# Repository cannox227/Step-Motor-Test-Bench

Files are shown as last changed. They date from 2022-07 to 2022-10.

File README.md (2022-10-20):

# Step-motor-test-bench

Step Motor Testbench is a tool made in collaboration with [ProM Facility](https://promfacility.eu/#/) which can be used to measure the __maximum power__ and the __maximum torque__ of a step motor. <br>
Notice that this is a prototype made up to validate the innovative company idea. 
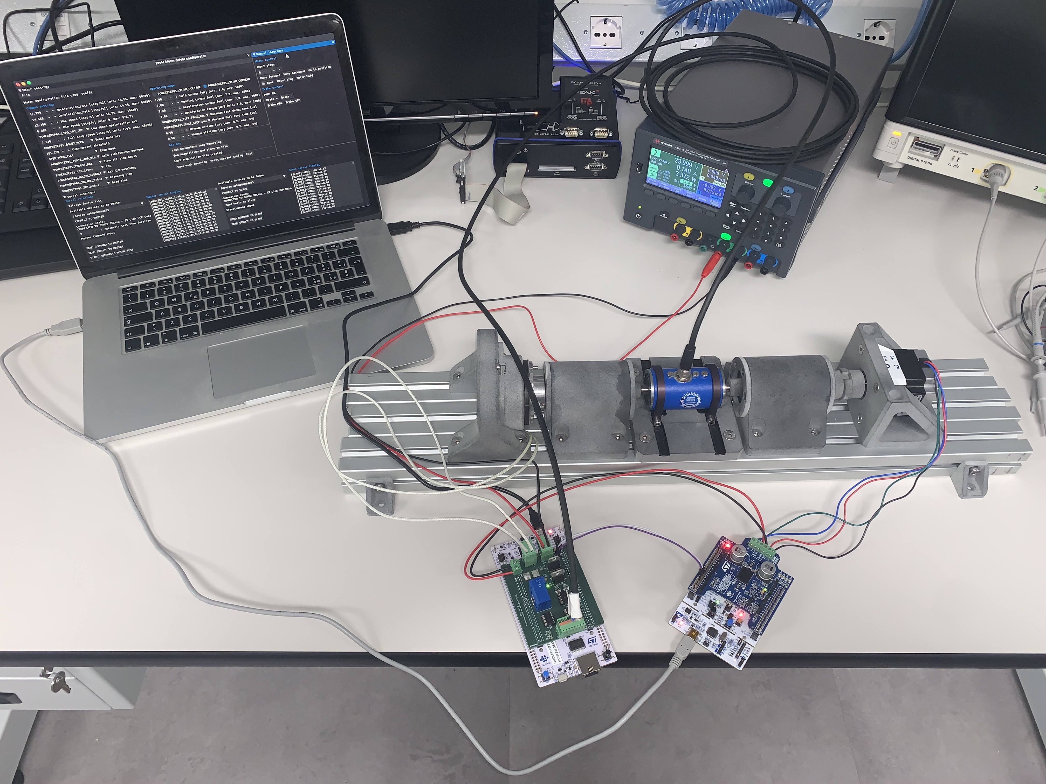
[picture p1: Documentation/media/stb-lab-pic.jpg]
stb-lab-pic


## Functionalities
1. Driving the stepper motor
2. Driving the magnetic brake
3. Measuring the involved physical quantities such as: torque, voltage and current of the motor
4. Set the motor driver parameters and show the plots related to the obtained motor curves using a GUI (Graphical User Interface)

## Main components
- Step motor (device under test)
- Torque sensor
- Magnetic brake
- Master unit made of
    - Nucleo STM32 F7 Board
    - Custom PCB to handle different voltages and conditionate the signals
- Slave unit made of
    - Nucleo STM32 F4 Board
    - STM X-NUCLEO-IHM03A1 stepper driver extension board

## System block diagram
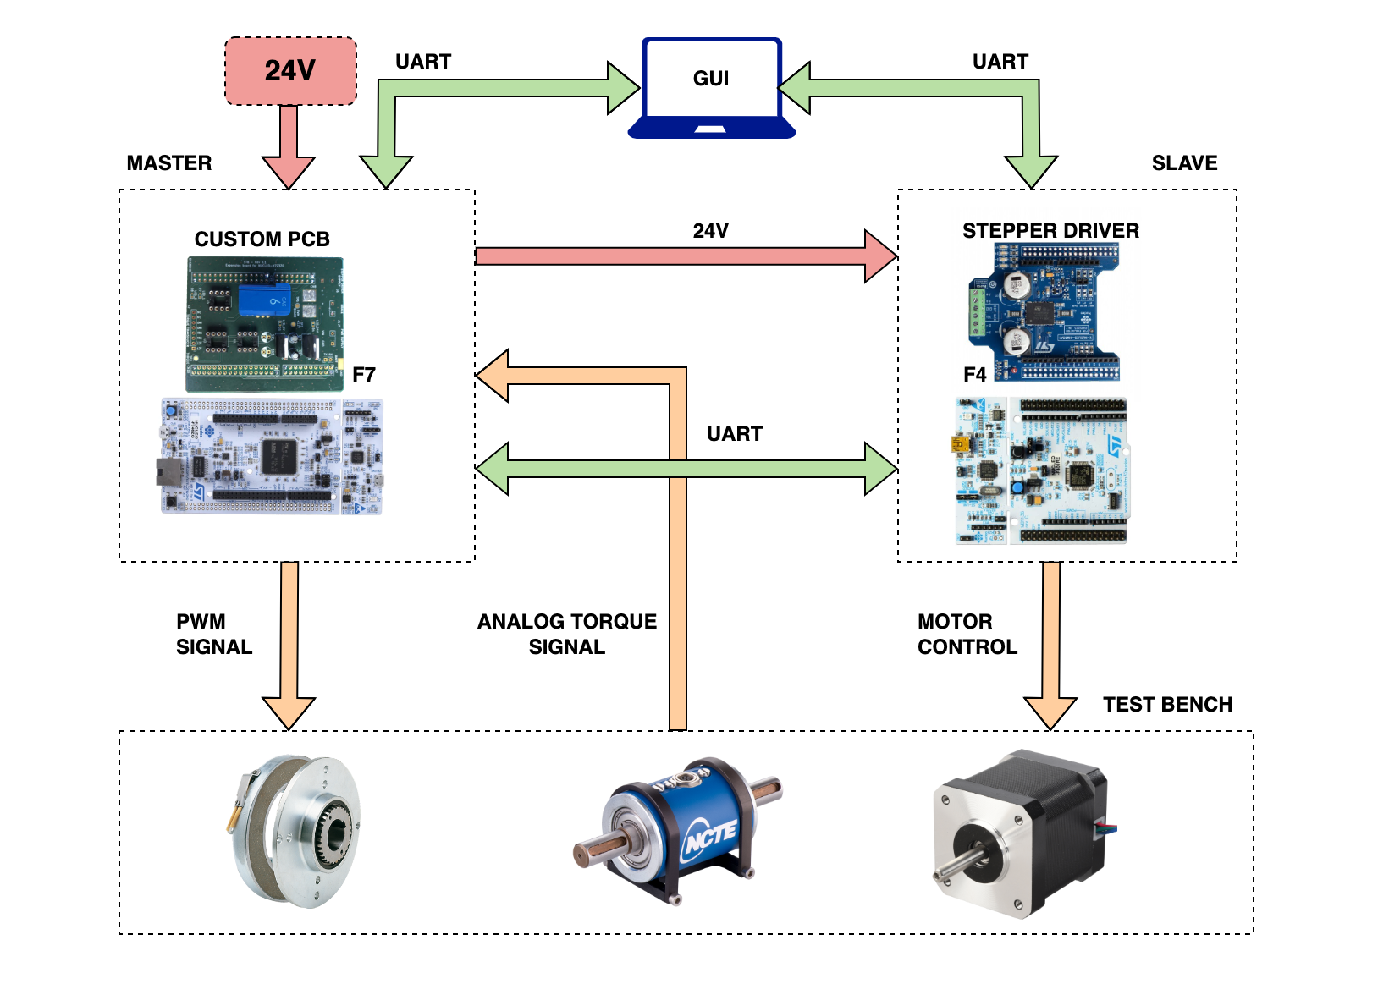
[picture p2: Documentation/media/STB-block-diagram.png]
System block diagram

## Thesis abstract
This thesis reports the work done during my internship period at ProM Facility, the company - based in Rovereto (TN) - is focused on mechanics, electronics and informatics prototyping. This work principally covers the high level software development and at the same time the baremetal firmware development to support the innovative company project. In particular, ProM Facility had the necessity to prototype a __stepper motor test bench__ for an internal usage. This measurement tool is able to determine the __maximum power__ and __maximum torque__ provided by the under test motor.

At my arrival in the company the test bench mechanical structure was already built, ensuring the connection between a magnetic brake, a torque sensor and a stepper motor. To make the prototype actually working it has been necessary to integrate the hardware development with the software one. Obtaining the characteristic curves that describes the performance of the motor has been one of the main objectives of my work, in order to get this results sensors of voltage, current and torque have been used. Moreover, a wide variety of motor driver parameters selection has been implemented, in such a way to build a custom configuration with the purpose of optimize the produced curves by operating on the single parameters. However, this curve optimization task will be studied by the future company interns.

It has also been developed a dedicated graphical user interface to let the end user interacting with the test bench, with this software it is possible to change the motor driver parameters and test it under load; on the other hand, to read the sensors values and drive the motor, two units have been projected: _master_ and _slave_. The first one is made up of a _STM Nucleo F7_ board with a custom developed _shield_, where sensors and signal conditioning circuits have been soldered. The second one, instead, is composed of a _STM Nucleo F4_ board and an expansion driver board - the _STM X-NUCLEO-IHM03A1_ - necessary to control the motor under the F4 _microcontroller_ rules.

The thesis especially describes the development process to create the graphical interface using the Python programming language and to write the firmware of the master unit. For the last one a duo formed by the STM Cube MX software and the C language has been selected. Eventually, the remaining work, consisting of the slave firmware development and the prototyping of the expansion board for the master unit, has been up to the colleague with whom I have shared the internship experience, _Lisa Santarossa_.

As planned, the project has been concluded successfully, gathering the curves of __torque-power__ based on the custom configuration chosen by the end user.

__You can find the theseis [here](/Documentation/Tommaso_Canova_STB_thesis.pdf)__

## Repo structure
    ├── 📁 Documentation    -> media and thesis
    ├── 📁 Firmware         -> slave and master units firmware
    ├── 📁 GUI              -> graphical user iterface and plot scripts
    └── 📁 Hardware         -> custom master unit expansion board kicad project

## GUI screenshots
The GUI is made up of two main windows: the first one is used to control the motor driver parameters, to test the motor under load, to communicate with both units using serial communication and to save the acquired data into a csv file. The second one is used to plot the acquired data into some.

The second one is used to read the sensors values and to plot the acquired data in a dynamic way. 

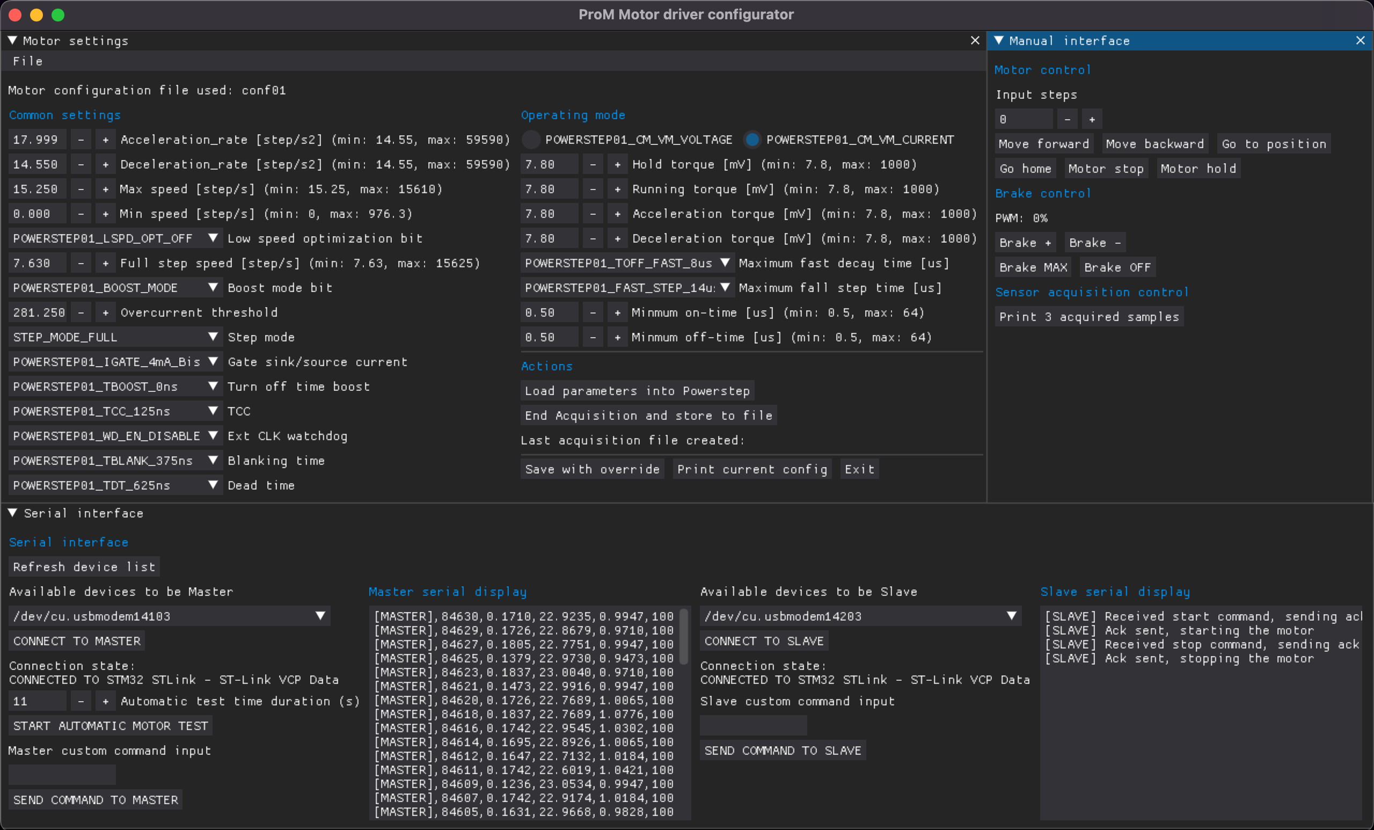
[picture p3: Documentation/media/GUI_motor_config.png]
GUI Motor config window


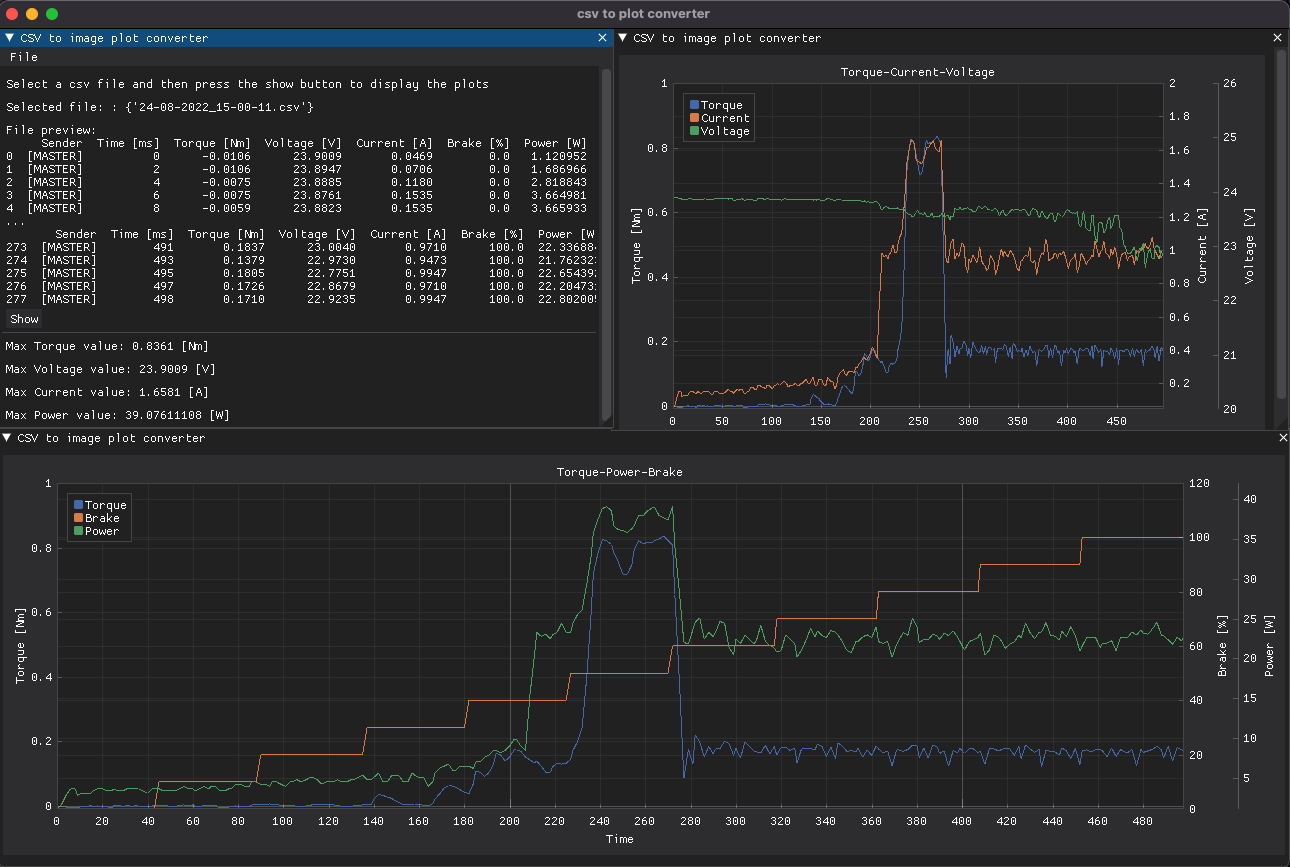
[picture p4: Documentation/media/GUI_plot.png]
GUI plot window


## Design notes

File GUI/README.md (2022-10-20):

# Stepper Testbench GUI
The GUI is made up of two main windows: the first one is used to control the motor driver parameters, to test the motor under load, to communicate with both units using serial communication and to save the acquired data into a csv file. The second one is used to plot the acquired data into some.

The second one is used to read the sensors values and to plot the acquired data in a dynamic way. 

GUI Motor config window

GUI plot window
# GUI Installation
    cd src
    pip3 install -r requirements.txt
# Usage
## Open STB motor dashboard
    python3 main.py

## Open CSV to plot handler
    python3 csv_to_plot_guy.py

## Store CSV datas into some pdf plots 
    cd csv
    python3 save_plot.py {csv_file.csv | last}

Note 1: The scripts takes one arguement which can be a csv (which contains the acquired) or the `last` keyword.
If `last` is typed, the script will take last added csv file inside `csv` folder.<br>
Note 2: The .csv file must be inside the `csv` folder and it has to respect the following format `DD_MM_YYYY_HH_MM_SS.csv`

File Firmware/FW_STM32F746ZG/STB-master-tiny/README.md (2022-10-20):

# STB master tiny
Just a fake playground to program a NUCLEO STMF4 board to test the communication logic. Nothing fancy here.

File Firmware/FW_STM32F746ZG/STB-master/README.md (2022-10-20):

# STB master
The StepperTestBench (STB) master unit is written in C using STM32CubeMX. The systems allows to control the magnetic brake and read the analog torque sensor. 
The master unit communicates both with the GUI and the slave unit using the serial UART protocol.

stb-schema

## Code Flowchart
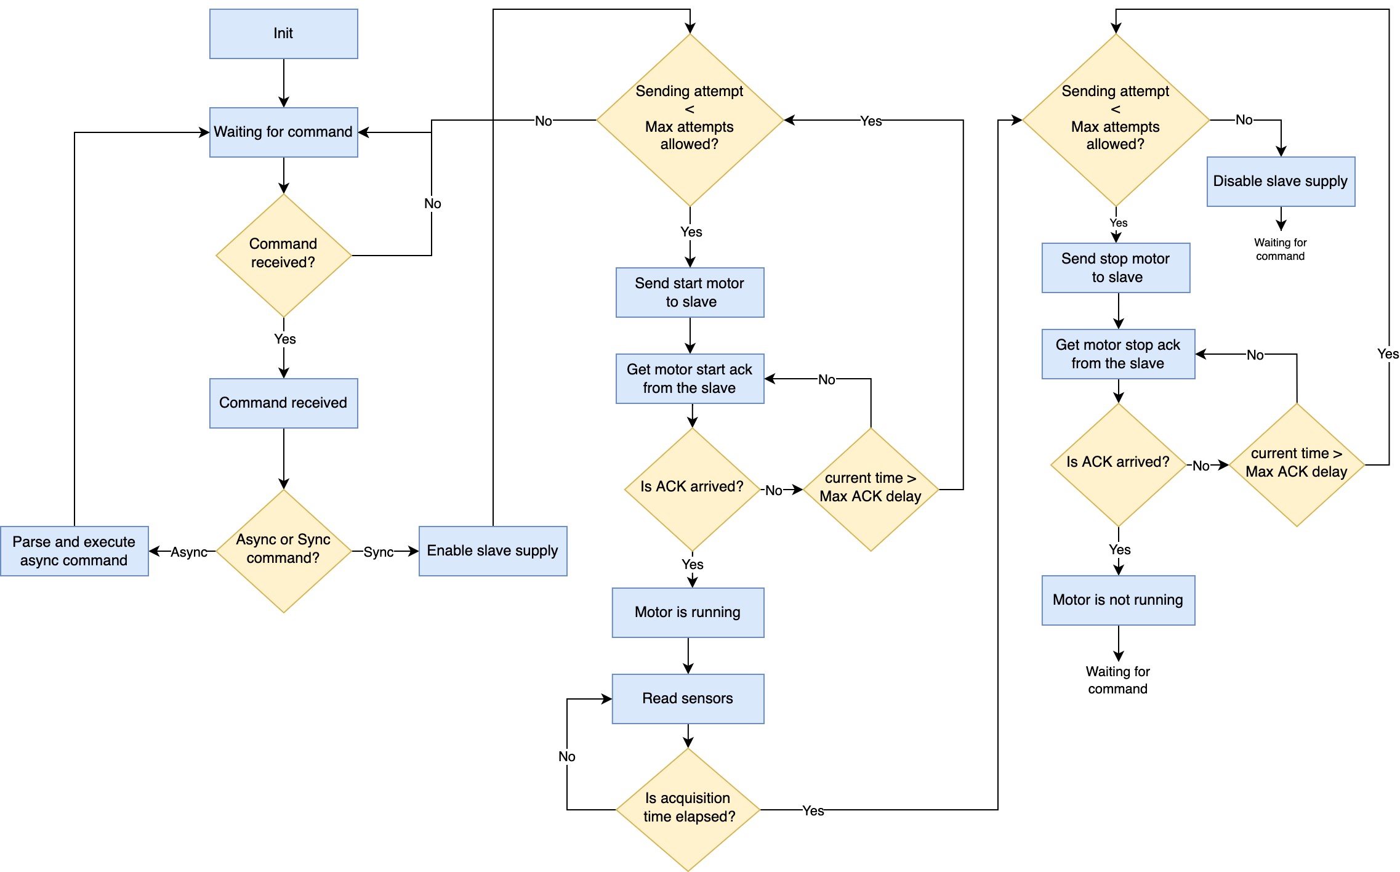
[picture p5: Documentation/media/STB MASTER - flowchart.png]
stb-master-flowchart


A finite-state machine (FSM) model has been chosen to describe and formalize the master unit be- haviour. Since the device has to deal with an __automatic test__ and a __manual test__, the FSM is basically divided in two sequential branches. The first one is aimed to handle a synchronous event (the automatic test), where every action of the unit is time dependent and at the same time is slave- message subordinate. To give an example, in the first branch it is not possible to read the analog sensors before the receiving of a `start-motor` message acknowledgment from the slave. On the other hand the second branch is __slave-independent__, so it is possible to manage a braking command or a reading sensors in an _asynchronous way_, without considering the current state of the slave. To give another example, during a manual test, it is possible to read the sensors or pilot the brake even when the slave is not driving the motor, as this branch is totally slave-independent. Note that a manual test has no need to start from a specific condition, indeed when the master is not operating an automatic test, every command is interpreted as a manual test command. The entire FSM flowchart is reported in figure 5.1.
When an automatic test is launched with the GUI, the master unit sends to the slave a `start_motor` command and then waits for a fixed time in order to receive an acknowledging message from the slave to know if the motor is running. The sending and waiting operation respects a fixed timing defined by the multiplication of the macros `MAX_CMD_SEND_ATTEMPTS` and `MAX_ACK_ALLOWED_DELAY_MS`. If the slave does not respect this timing, the test must be re-launched by the GUI; otherwise if it is respected, the master starts to acquire the ADCs values and sends them to the GUI, while piloting gradually the brake, until the total duration of the test. Then the brake is released and a `stop_motor` command is sent with the same acknowledgement procedure.

## Build and flash the project
Open the project with VSCode and install the [stm32-for-vscode](https://marketplace.visualstudio.com/items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,STM32%20for%20VSCode%20configuration%20file.) extension.

The you can just use the Build button and the Flash one to upload the firmware.
build-flash-gif

_This gif is taken from the stm32-for-vscode extension_

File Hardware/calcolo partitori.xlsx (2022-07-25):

Dispositivo | Vmin | Vmax | V_max_scelta | V_in_max_adc | V_in_max_adc/V_max_scelta | R1 | R2 | R2/(R1+R2) | V_in_adc_post_partitore
Torsiometro | 0.5 | 4.5 | 5 | 3.3 | 0.66 | 3.3 | 6.2 | 0.6526315789 | 3.263157895 | VMAX
Sensore di corrente | 0.375 | 4.625 | 5 | 3.3 | 0.66 | 3.3 | 6.2 | 0.6526315789 | 3.263157895
Tensione banco/batteria | 0 | 24 | 24 | 3.3 | 0.1375 | 6.2 | 1 | 0.1388888889 | 3.333333333 | R1

OpAmp | R1 | R2 | 2*R1/(R2+2R1) | Vmax_adc/V_in_max |  |  |  |  |  | --------> | VOUT
-2*R1/(R2+2R1) = 0.66 | 6.8 | 8.2 | 0.623853211 | 0.66 | Torsiometro + Sensore di Corrente
 | 1 | 18 | 0.1 | 0.11 | Tensione banco/batteria |  |  |  |  | R2

 |  |  |  |  |  |  |  |  |  | GND
Torsiometro lavora a 12 |  |  |  |  |  |  |  |  |  | VMAX*R2/(R1+R2) = 3.3
30 -> 12
12 -> 5 |  |  |  |  |  |  |  |  |  | 3.3/VMAX = R2/(R1+R2)
Regolatore | vo | vref | r2 | r1 | r2/r1 | vo/vref -1
Vo = Vref*(1+r2/r1) | 12 | 1.25 | 8.6 | 1 | 8.6 | 8.6

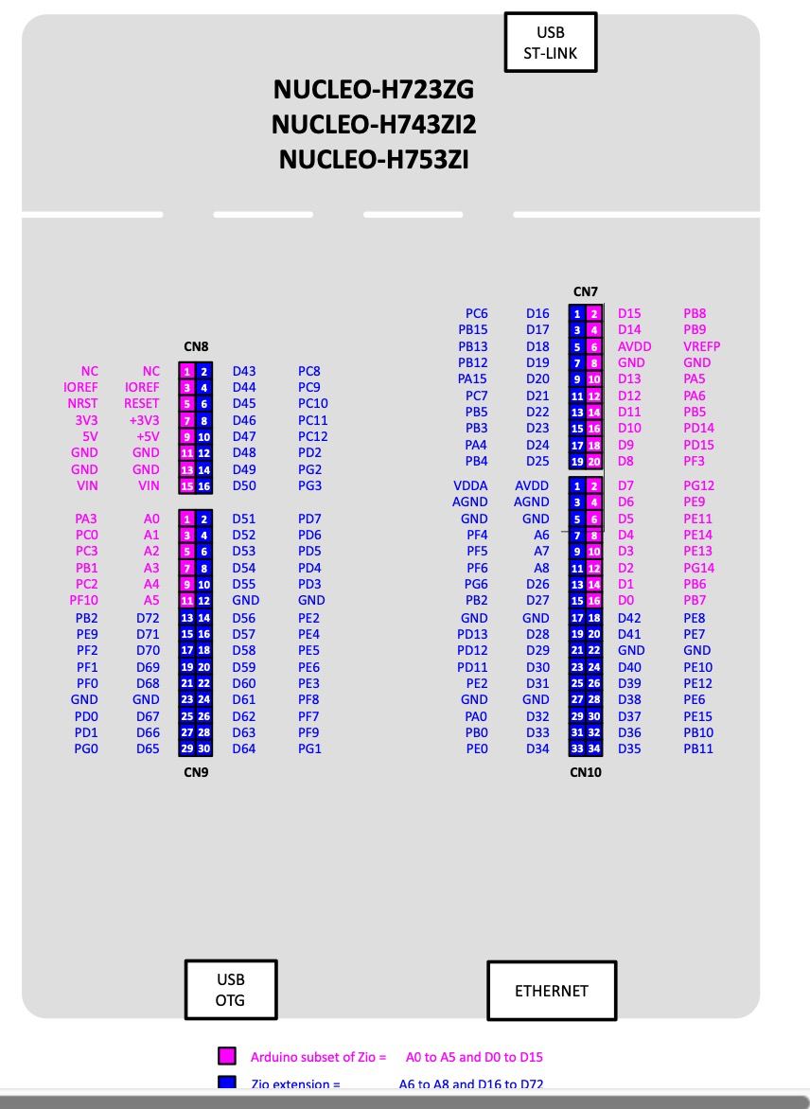
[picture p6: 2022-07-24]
Hardware/datasheets/STM32H723ZG PINOUT.jpeg

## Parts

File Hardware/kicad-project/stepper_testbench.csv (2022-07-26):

Source: | /Users/tommasocanova/Desktop/UNI/TESI/Step-Motor-Test-Bench/Hardware/kicad-project/stepper_testbench.kicad_sch
Date: | 2022 July 26, Tuesday 16:24:27
Tool: | Eeschema (6.0.2-0)
Generator: | /Applications/KiCad/KiCad.app/Contents/SharedSupport/plugins/bom_csv_grouped_by_value.py
Component Count: | 77
Individual Components:
Item | Qty | Reference(s) | Value | LibPart | Footprint | Datasheet | Spice_Netlist_Enabled | Spice_Primitive | V
 |  | C1 | 100n | Device:C | Capacitor_SMD:C_0603_1608Metric | ~
 |  | C2 | 0.1u | Device:C | Capacitor_SMD:C_0603_1608Metric | ~
 |  | C3 | 0.1u | Device:C | Capacitor_SMD:C_0603_1608Metric | ~
 |  | C4 | 100n | Device:C | Capacitor_SMD:C_0603_1608Metric | ~
 |  | C5 | 0.1u | Device:C | Capacitor_SMD:C_0603_1608Metric | ~
 |  | C6 | 100n | Device:C | Capacitor_SMD:C_0603_1608Metric | ~
 |  | C7 | 0.1u | Device:C | Capacitor_SMD:C_0603_1608Metric | ~
 |  | C8 | 0.33u | Device:C | Capacitor_SMD:C_0603_1608Metric | ~ |  |  | 25V
 |  | C9 | DNP | Device:C | Capacitor_SMD:C_0805_2012Metric | ~
 |  | C10 | 0.33u | Device:C | Capacitor_SMD:C_0603_1608Metric | ~ |  |  | 25V
 |  | C11 | 0.1u | Device:C | Capacitor_SMD:C_0603_1608Metric | ~
 |  | C12 | 0.1u | Device:C | Capacitor_SMD:C_0603_1608Metric | ~ |  |  | 25V
 |  | C13 | 0.33u_DNP | Device:C | Capacitor_THT:CP_Radial_D5.0mm_P2.50mm | ~ |  |  | 25V
 |  | C14 | 0.1u_DNP | Device:C | Capacitor_THT:CP_Radial_D5.0mm_P2.50mm | ~ |  |  | 25V
 |  | C15 | 0.33u_DNP | Device:C | Capacitor_THT:CP_Radial_D5.0mm_P2.50mm | ~ |  |  | 25V
 |  | C16 | 0.1u_DNP | Device:C | Capacitor_THT:CP_Radial_D5.0mm_P2.50mm | ~ |  |  | 25V
 |  | C17 | C | Device:C | Capacitor_SMD:C_0805_2012Metric | ~
 |  | C18 | C | Device:C | Capacitor_SMD:C_0805_2012Metric | ~
 |  | C19 | C | Device:C | Capacitor_SMD:C_0805_2012Metric | ~
 |  | CN7 | Conn_02x10_Odd_Even | Connector_Generic:Conn_02x10_Odd_Even | Connector_PinHeader_2.54mm:PinHeader_2x10_P2.54mm_Vertical | ~
 |  | CN8 | Conn_02x08_Odd_Even | Connector_Generic:Conn_02x08_Odd_Even | Connector_PinHeader_2.54mm:PinHeader_2x08_P2.54mm_Vertical | ~
 |  | CN9 | Conn_02x15_Odd_Even | Connector_Generic:Conn_02x15_Odd_Even | Connector_PinHeader_2.54mm:PinHeader_2x15_P2.54mm_Vertical | ~
 |  | CN10 | Conn_02x17_Odd_Even | Connector_Generic:Conn_02x17_Odd_Even | Connector_PinHeader_2.54mm:PinHeader_2x17_P2.54mm_Vertical | ~
 |  | D1 | DIODE | Simulation_SPICE:DIODE | Diode_SMD:D_SOD-323 | ~ | Y | D
 |  | D2 | DIODE | Simulation_SPICE:DIODE | Diode_SMD:D_SOD-323 | ~ | Y | D
 |  | D3 | D_Zener | Device:D_Zener | Diode_SMD:D_SOD-323 | ~
 |  | D4 | LED_RED | Device:LED | LED_SMD:LED_0603_1608Metric | ~
 |  | D5 | DIODE | Simulation_SPICE:DIODE | Diode_SMD:D_SOD-323 | ~ | Y | D
 |  | D6 | LED_GREEN | Device:LED | LED_SMD:LED_0603_1608Metric | ~
 |  | D7 | LED | Device:LED | LED_SMD:LED_0603_1608Metric | ~
 |  | D8 | LED | Device:LED | LED_SMD:LED_0603_1608Metric | ~
 |  | FB1 | FerriteBead | Device:FerriteBead | Resistor_SMD:R_0805_2012Metric | ~
 |  | J1 | Brake connector | Connector_Generic:Conn_01x02 | Connector_PinHeader_2.54mm:PinHeader_1x02_P2.54mm_Vertical | ~
 |  | J2 | Conn_01x08 | Connector_Generic:Conn_01x08 | Connector_PinHeader_2.54mm:PinHeader_1x08_P2.54mm_Vertical | ~
 |  | J3 | PWM module connector | Connector_Generic:Conn_01x03 | Connector_PinHeader_2.54mm:PinHeader_1x03_P2.54mm_Vertical | ~
 |  | J4 | Conn_01x02 | Connector_Generic:Conn_01x02 | Connector_PinHeader_2.54mm:PinHeader_1x02_P2.54mm_Vertical | ~
 |  | J5 | UART Connector | Connector_Generic:Conn_01x02 | Connector_PinHeader_2.54mm:PinHeader_1x02_P2.54mm_Vertical | ~
 |  | J6 | Stepper supply | Connector_Generic:Conn_01x02 | Connector_PinHeader_2.54mm:PinHeader_1x02_P2.54mm_Vertical | ~
 |  | Q1 | Q_NMOS_DGS | Device:Q_NMOS_GDS | Package_TO_SOT_SMD:TO-252-2 | ~
 |  | R1 | 10k | Device:R | Resistor_SMD:R_0603_1608Metric | ~
 |  | R2 | 0 | Device:R | Resistor_SMD:R_0603_1608Metric | ~
 |  | R3 | 47 | Device:R | Resistor_SMD:R_0603_1608Metric | ~
 |  | R4 | 0 | Device:R | Resistor_SMD:R_0603_1608Metric | ~
 |  | R5 | 0 | Device:R | Resistor_SMD:R_0603_1608Metric | ~
 |  | R6 | 10k | Device:R | Resistor_SMD:R_0603_1608Metric | ~
 |  | R7 | 330k | Device:R | Resistor_SMD:R_0603_1608Metric | ~
 |  | R8 | 620k | Device:R | Resistor_SMD:R_0603_1608Metric | ~
 |  | R9 | 10k | Device:R | Resistor_SMD:R_0603_1608Metric | ~
 |  | R10 | 330k | Device:R | Resistor_SMD:R_0603_1608Metric | ~
 |  | R11 | 620k | Device:R | Resistor_SMD:R_0603_1608Metric | ~
 |  | R12 | 10k | Device:R | Resistor_SMD:R_0603_1608Metric | ~
 |  | R13 | 620k | Device:R | Resistor_SMD:R_0603_1608Metric | ~
 |  | R14 | 100k | Device:R | Resistor_SMD:R_0603_1608Metric | ~
 |  | R15 | 0 | Device:R | Resistor_SMD:R_0603_1608Metric | ~
 |  | R16 | R | Device:R | Resistor_SMD:R_0603_1608Metric | ~
 |  | R17 | R | Device:R | Resistor_SMD:R_0603_1608Metric | ~
 |  | R18 | 510 | Device:R | Resistor_SMD:R_0603_1608Metric | ~
 |  | R19 | 330 | Device:R | Resistor_SMD:R_0603_1608Metric | ~
 |  | R20 | 5k1 | Device:R | Resistor_SMD:R_0603_1608Metric | ~
 |  | R21 | 1k | Device:R | Resistor_SMD:R_0603_1608Metric | ~
 |  | R22 | 0 | Device:R | Resistor_SMD:R_0603_1608Metric | ~
 |  | R23 | R | Device:R | Resistor_SMD:R_0603_1608Metric | ~
 |  | R24 | R | Device:R | Resistor_SMD:R_0603_1608Metric | ~
 |  | R25 | 0 | Device:R | Resistor_SMD:R_0603_1608Metric | ~
 |  | R26 | R | Device:R | Resistor_SMD:R_0603_1608Metric | ~
 |  | R27 | R | Device:R | Resistor_SMD:R_0603_1608Metric | ~
 |  | TP1 | 24V | Connector:TestPoint | TestPoint:TestPoint_Pad_D2.0mm | ~
 |  | TP2 | TORQUE | Connector:TestPoint | TestPoint:TestPoint_Pad_D2.0mm | ~
 |  | TP3 | 12V | Connector:TestPoint | TestPoint:TestPoint_Pad_D2.0mm | ~
 |  | TP4 | 5V | Connector:TestPoint | TestPoint:TestPoint_Pad_D2.0mm | ~
 |  | TP5 | BRAKE | Connector:TestPoint | TestPoint:TestPoint_Pad_D2.0mm | ~
 |  | U1 | LM358P | EncoderLib:LM358P | Package_DIP:DIP-8_W7.62mm | https://www.ti.com/lit/ds/symlink/lm358.pdf?ts=1658579670969
 |  | U2 | LEM-CAS-6NP | Sensing lib:LEM-CAS-6-NP | Sensing lib:LEM-CAS-6-NP | https://www.lem.com/sites/default/files/products_datasheets/cas_series.pdf
 |  | U3 | LM358P | EncoderLib:LM358P | Package_DIP:DIP-8_W7.62mm | https://www.ti.com/lit/ds/symlink/lm358.pdf?ts=1658579670969
 |  | U4 | LM358P | EncoderLib:LM358P | Package_DIP:DIP-8_W7.62mm | https://www.ti.com/lit/ds/symlink/lm358.pdf?ts=1658579670969
 |  | U5 | LM7812_TO220 | Regulator_Linear:LM7812_TO220 | Package_TO_SOT_THT:TO-220-3_Vertical | https://www.onsemi.cn/PowerSolutions/document/MC7800-D.PDF
 |  | U6 | L7805 | Regulator_Linear:L7805 | Package_TO_SOT_THT:TO-220-3_Vertical | http://www.st.com/content/ccc/resource/technical/document/datasheet/41/4f/b3/b0/12/d4/47/88/CD00000444.pdf/files/CD00000444.pdf/jcr:content/translations/en.CD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
Collated Components:
Item | Qty | Reference(s) | Value | LibPart | Footprint | Datasheet | Spice_Netlist_Enabled | Spice_Primitive | V
1 | 3 | C1, C4, C6 | 100n | Device:C | Capacitor_SMD:C_0603_1608Metric | ~
2 | 6 | C2, C3, C5, C7, C11, C12 | 0.1u | Device:C | Capacitor_SMD:C_0603_1608Metric | ~ |  |  | 25V
3 | 2 | C8, C10 | 0.33u | Device:C | Capacitor_SMD:C_0603_1608Metric | ~ |  |  | 25V
4 | 1 | C9 | DNP | Device:C | Capacitor_SMD:C_0805_2012Metric | ~
5 | 2 | C13, C15 | 0.33u_DNP | Device:C | Capacitor_THT:CP_Radial_D5.0mm_P2.50mm | ~ |  |  | 25V
6 | 2 | C14, C16 | 0.1u_DNP | Device:C | Capacitor_THT:CP_Radial_D5.0mm_P2.50mm | ~ |  |  | 25V
7 | 3 | C17, C18, C19 | C | Device:C | Capacitor_SMD:C_0805_2012Metric | ~
8 | 1 | CN7 | Conn_02x10_Odd_Even | Connector_Generic:Conn_02x10_Odd_Even | Connector_PinHeader_2.54mm:PinHeader_2x10_P2.54mm_Vertical | ~
9 | 1 | CN8 | Conn_02x08_Odd_Even | Connector_Generic:Conn_02x08_Odd_Even | Connector_PinHeader_2.54mm:PinHeader_2x08_P2.54mm_Vertical | ~
10 | 1 | CN9 | Conn_02x15_Odd_Even | Connector_Generic:Conn_02x15_Odd_Even | Connector_PinHeader_2.54mm:PinHeader_2x15_P2.54mm_Vertical | ~
11 | 1 | CN10 | Conn_02x17_Odd_Even | Connector_Generic:Conn_02x17_Odd_Even | Connector_PinHeader_2.54mm:PinHeader_2x17_P2.54mm_Vertical | ~
12 | 3 | D1, D2, D5 | DIODE | Simulation_SPICE:DIODE | Diode_SMD:D_SOD-323 | ~ | Y | D
13 | 1 | D3 | D_Zener | Device:D_Zener | Diode_SMD:D_SOD-323 | ~
14 | 1 | D4 | LED_RED | Device:LED | LED_SMD:LED_0603_1608Metric | ~
15 | 1 | D6 | LED_GREEN | Device:LED | LED_SMD:LED_0603_1608Metric | ~
16 | 2 | D7, D8 | LED | Device:LED | LED_SMD:LED_0603_1608Metric | ~
17 | 1 | FB1 | FerriteBead | Device:FerriteBead | Resistor_SMD:R_0805_2012Metric | ~
18 | 1 | J1 | Brake connector | Connector_Generic:Conn_01x02 | Connector_PinHeader_2.54mm:PinHeader_1x02_P2.54mm_Vertical | ~
19 | 1 | J2 | Conn_01x08 | Connector_Generic:Conn_01x08 | Connector_PinHeader_2.54mm:PinHeader_1x08_P2.54mm_Vertical | ~
20 | 1 | J3 | PWM module connector | Connector_Generic:Conn_01x03 | Connector_PinHeader_2.54mm:PinHeader_1x03_P2.54mm_Vertical | ~
21 | 1 | J4 | Conn_01x02 | Connector_Generic:Conn_01x02 | Connector_PinHeader_2.54mm:PinHeader_1x02_P2.54mm_Vertical | ~
22 | 1 | J5 | UART Connector | Connector_Generic:Conn_01x02 | Connector_PinHeader_2.54mm:PinHeader_1x02_P2.54mm_Vertical | ~
23 | 1 | J6 | Stepper supply | Connector_Generic:Conn_01x02 | Connector_PinHeader_2.54mm:PinHeader_1x02_P2.54mm_Vertical | ~
24 | 1 | Q1 | Q_NMOS_DGS | Device:Q_NMOS_GDS | Package_TO_SOT_SMD:TO-252-2 | ~
25 | 4 | R1, R6, R9, R12 | 10k | Device:R | Resistor_SMD:R_0603_1608Metric | ~
26 | 6 | R2, R4, R5, R15, R22, R25 | 0 | Device:R | Resistor_SMD:R_0603_1608Metric | ~
27 | 1 | R3 | 47 | Device:R | Resistor_SMD:R_0603_1608Metric | ~
28 | 2 | R7, R10 | 330k | Device:R | Resistor_SMD:R_0603_1608Metric | ~
29 | 3 | R8, R11, R13 | 620k | Device:R | Resistor_SMD:R_0603_1608Metric | ~
30 | 1 | R14 | 100k | Device:R | Resistor_SMD:R_0603_1608Metric | ~
31 | 6 | R16, R17, R23, R24, R26, R27 | R | Device:R | Resistor_SMD:R_0603_1608Metric | ~
32 | 1 | R18 | 510 | Device:R | Resistor_SMD:R_0603_1608Metric | ~
33 | 1 | R19 | 330 | Device:R | Resistor_SMD:R_0603_1608Metric | ~
34 | 1 | R20 | 5k1 | Device:R | Resistor_SMD:R_0603_1608Metric | ~
35 | 1 | R21 | 1k | Device:R | Resistor_SMD:R_0603_1608Metric | ~
36 | 1 | TP1 | 24V | Connector:TestPoint | TestPoint:TestPoint_Pad_D2.0mm | ~
37 | 1 | TP2 | TORQUE | Connector:TestPoint | TestPoint:TestPoint_Pad_D2.0mm | ~
38 | 1 | TP3 | 12V | Connector:TestPoint | TestPoint:TestPoint_Pad_D2.0mm | ~
39 | 1 | TP4 | 5V | Connector:TestPoint | TestPoint:TestPoint_Pad_D2.0mm | ~
40 | 1 | TP5 | BRAKE | Connector:TestPoint | TestPoint:TestPoint_Pad_D2.0mm | ~
41 | 3 | U1, U3, U4 | LM358P | EncoderLib:LM358P | Package_DIP:DIP-8_W7.62mm | https://www.ti.com/lit/ds/symlink/lm358.pdf?ts=1658579670969
42 | 1 | U2 | LEM-CAS-6NP | Sensing lib:LEM-CAS-6-NP | Sensing lib:LEM-CAS-6-NP | https://www.lem.com/sites/default/files/products_datasheets/cas_series.pdf
43 | 1 | U5 | LM7812_TO220 | Regulator_Linear:LM7812_TO220 | Package_TO_SOT_THT:TO-220-3_Vertical | https://www.onsemi.cn/PowerSolutions/document/MC7800-D.PDF
44 | 1 | U6 | L7805 | Regulator_Linear:L7805 | Package_TO_SOT_THT:TO-220-3_Vertical | http://www.st.com/content/ccc/resource/technical/document/datasheet/41/4f/b3/b0/12/d4/47/88/CD00000444.pdf/files/CD00000444.pdf/jcr:content/translations/en.CD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

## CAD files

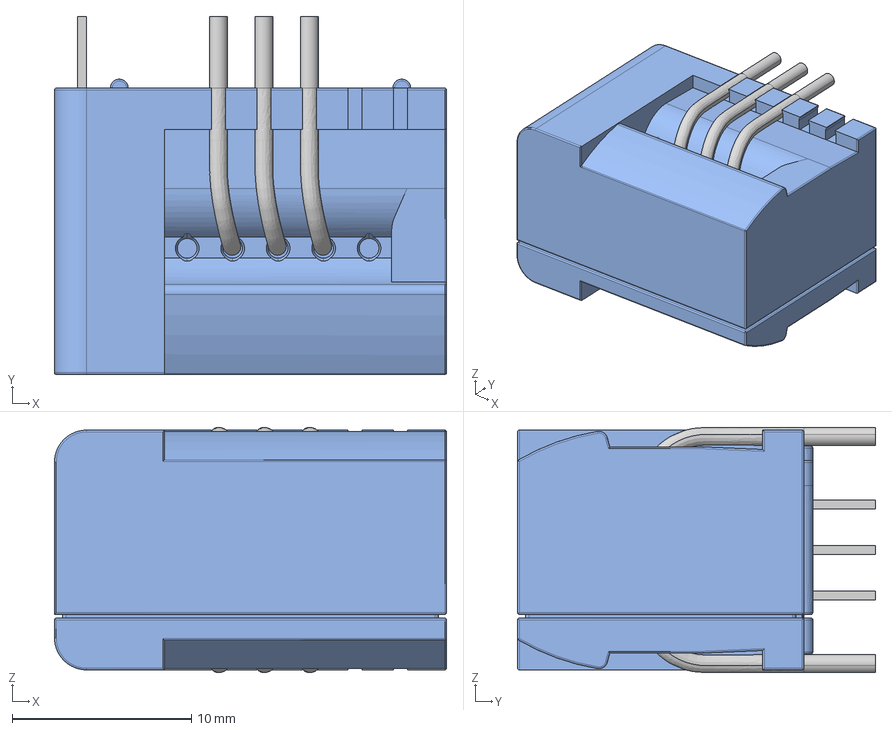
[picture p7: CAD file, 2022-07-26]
Hardware/kicad-project/kicad-lib/3d-models/CAS 6-15-25-50-NP Blackbox.stp
21.9 x 20.0 x 13.7 mm
1.Case
sec1 x 3
jumper.4 x 3

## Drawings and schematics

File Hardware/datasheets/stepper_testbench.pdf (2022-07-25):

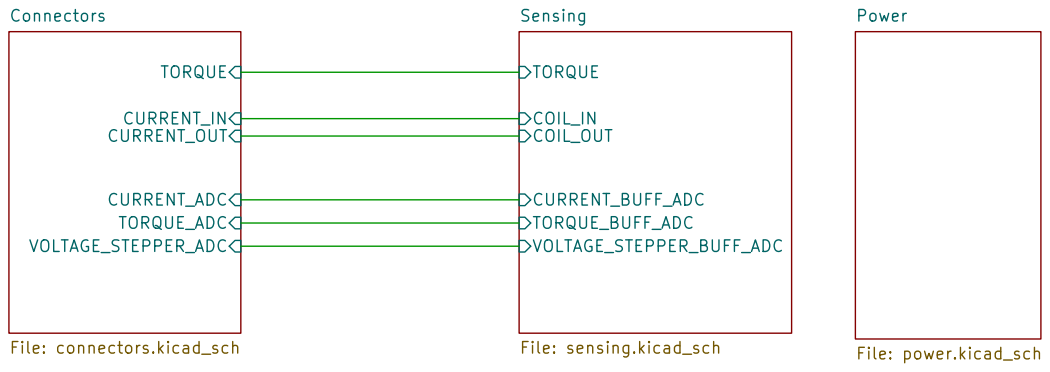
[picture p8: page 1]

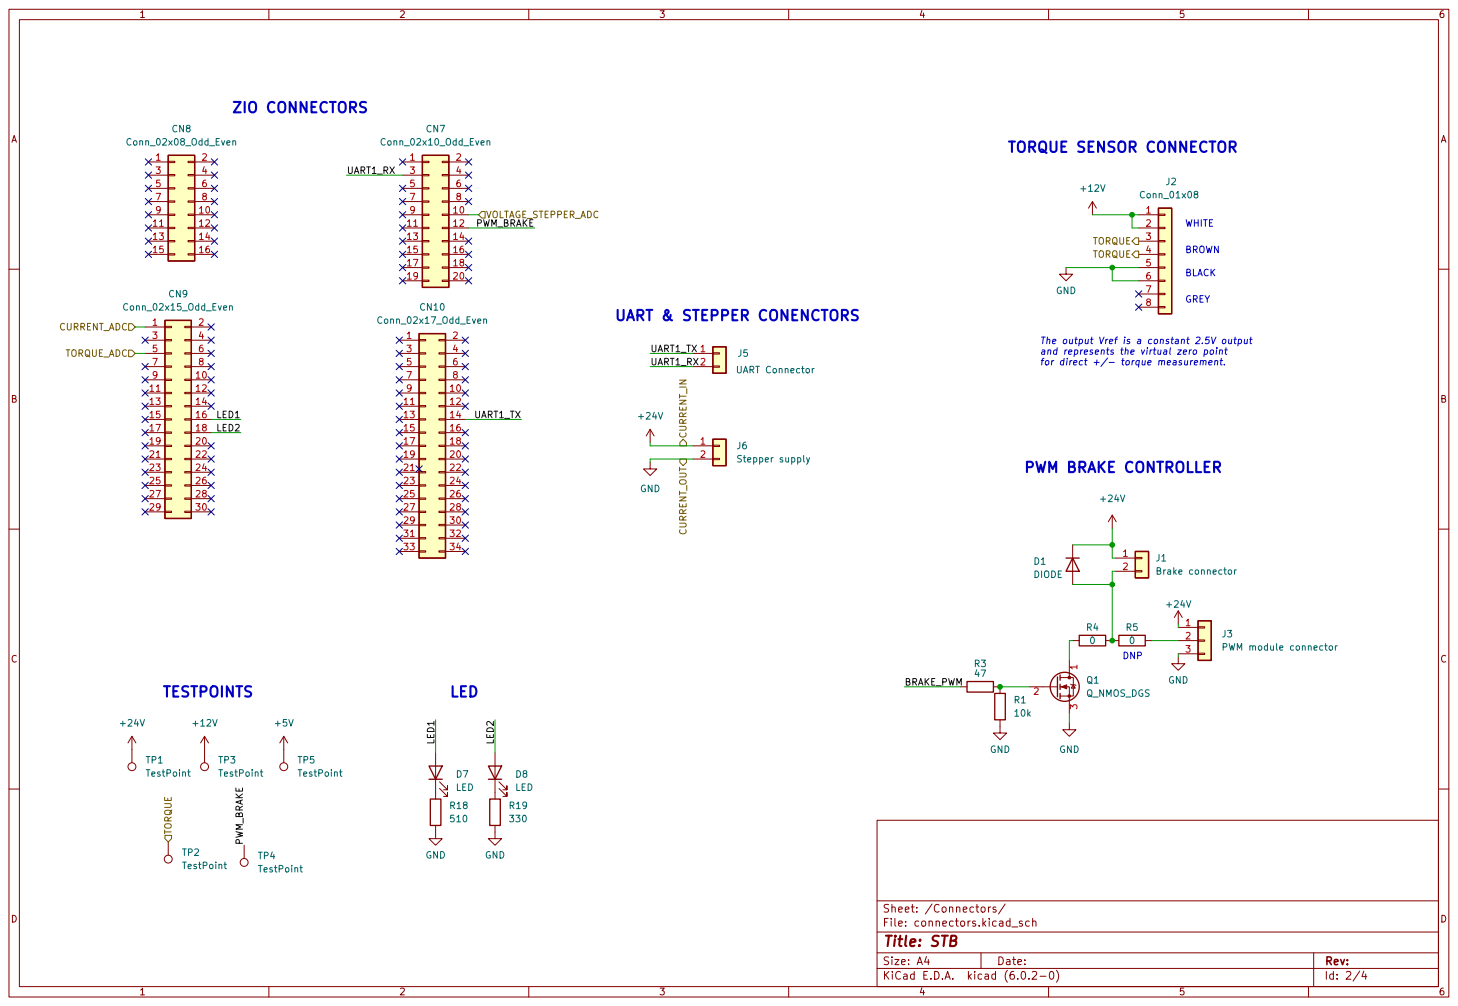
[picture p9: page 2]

The output Vref is a constant 2.5V output
and represents the virtual zero point
for direct +/- torque measurement.

File: connectors.kicad_sch Sheet: /Connectors/
Id: 2/4 Title: STB

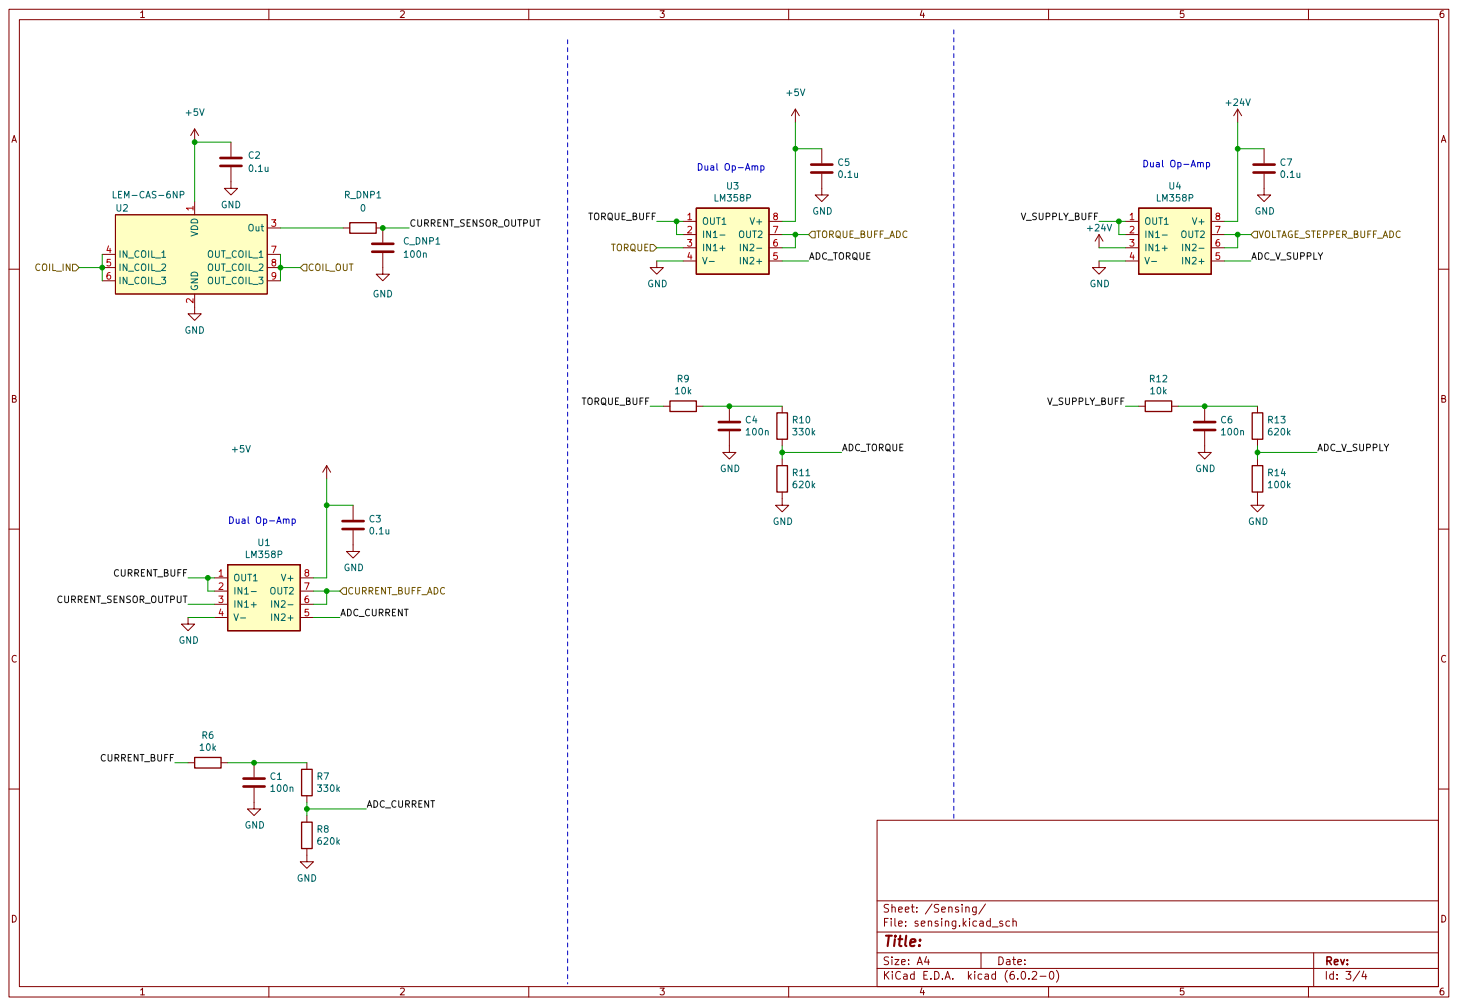
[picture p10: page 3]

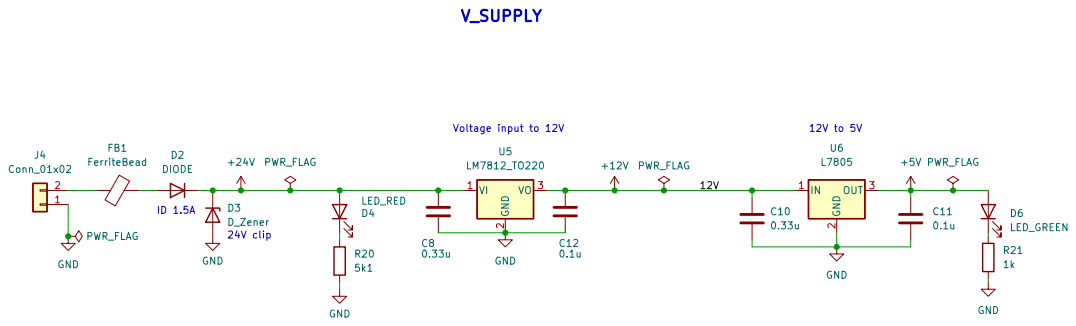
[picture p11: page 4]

File: power.kicad_sch Sheet: /Power/ GND

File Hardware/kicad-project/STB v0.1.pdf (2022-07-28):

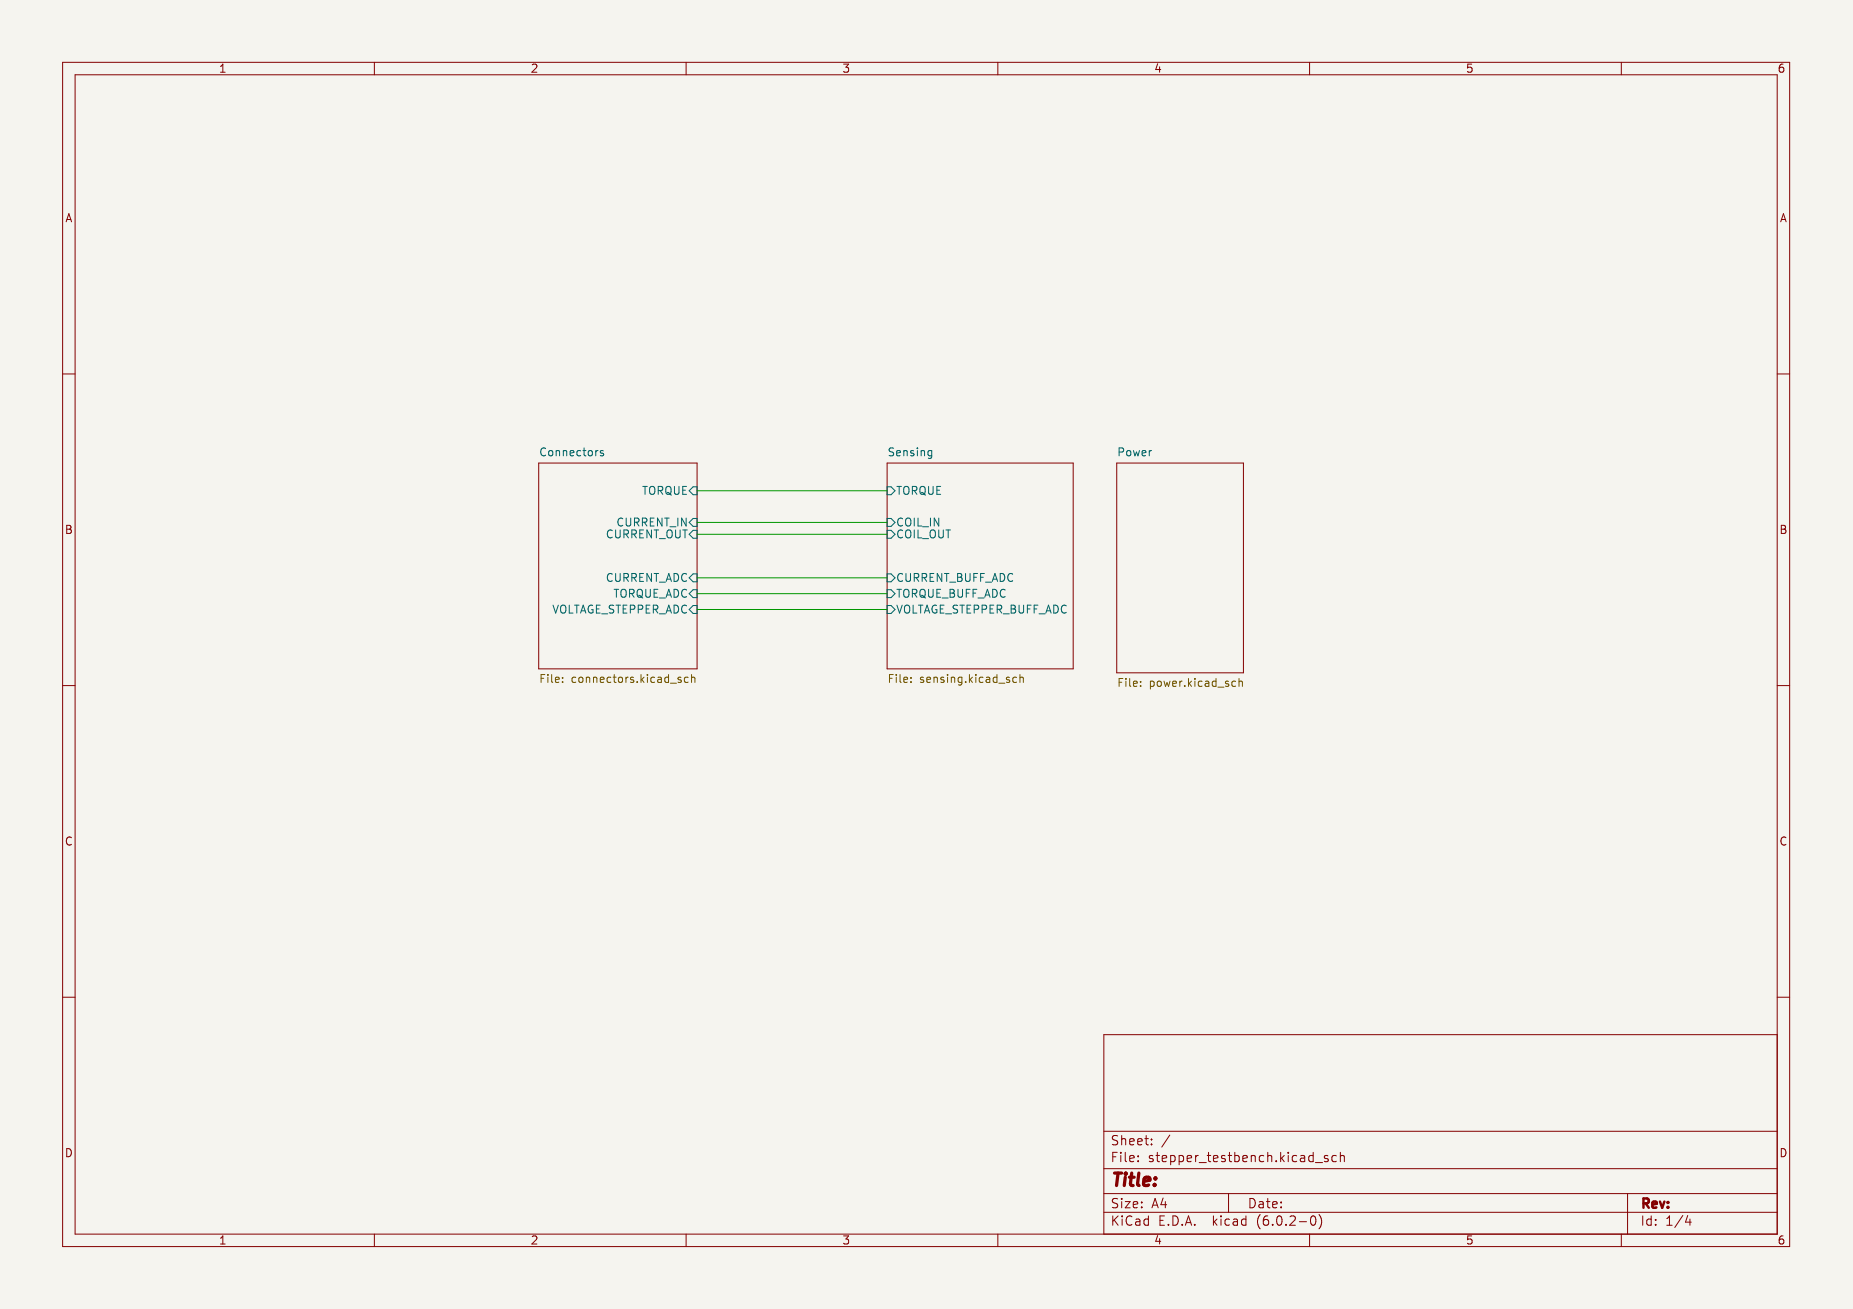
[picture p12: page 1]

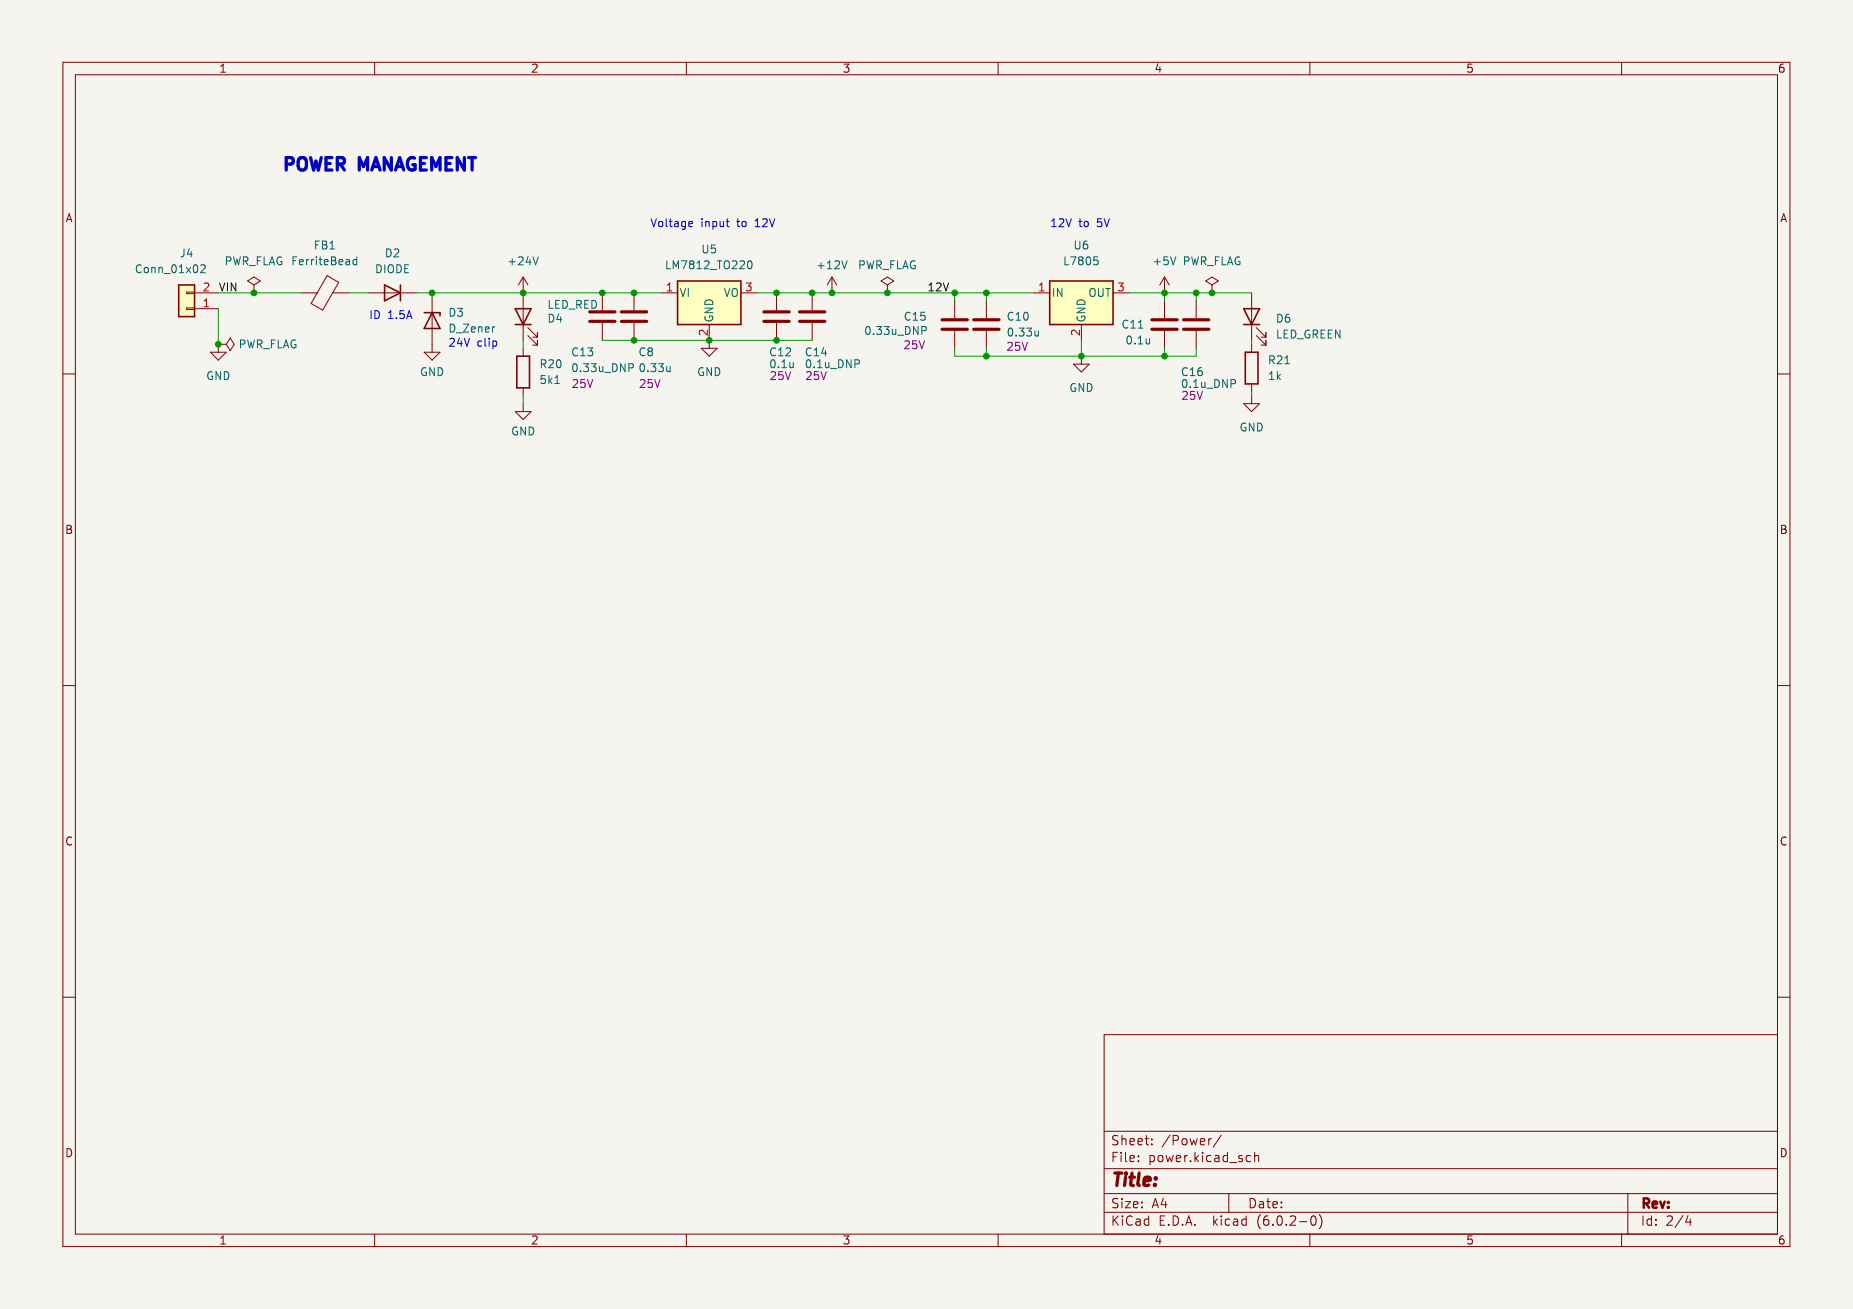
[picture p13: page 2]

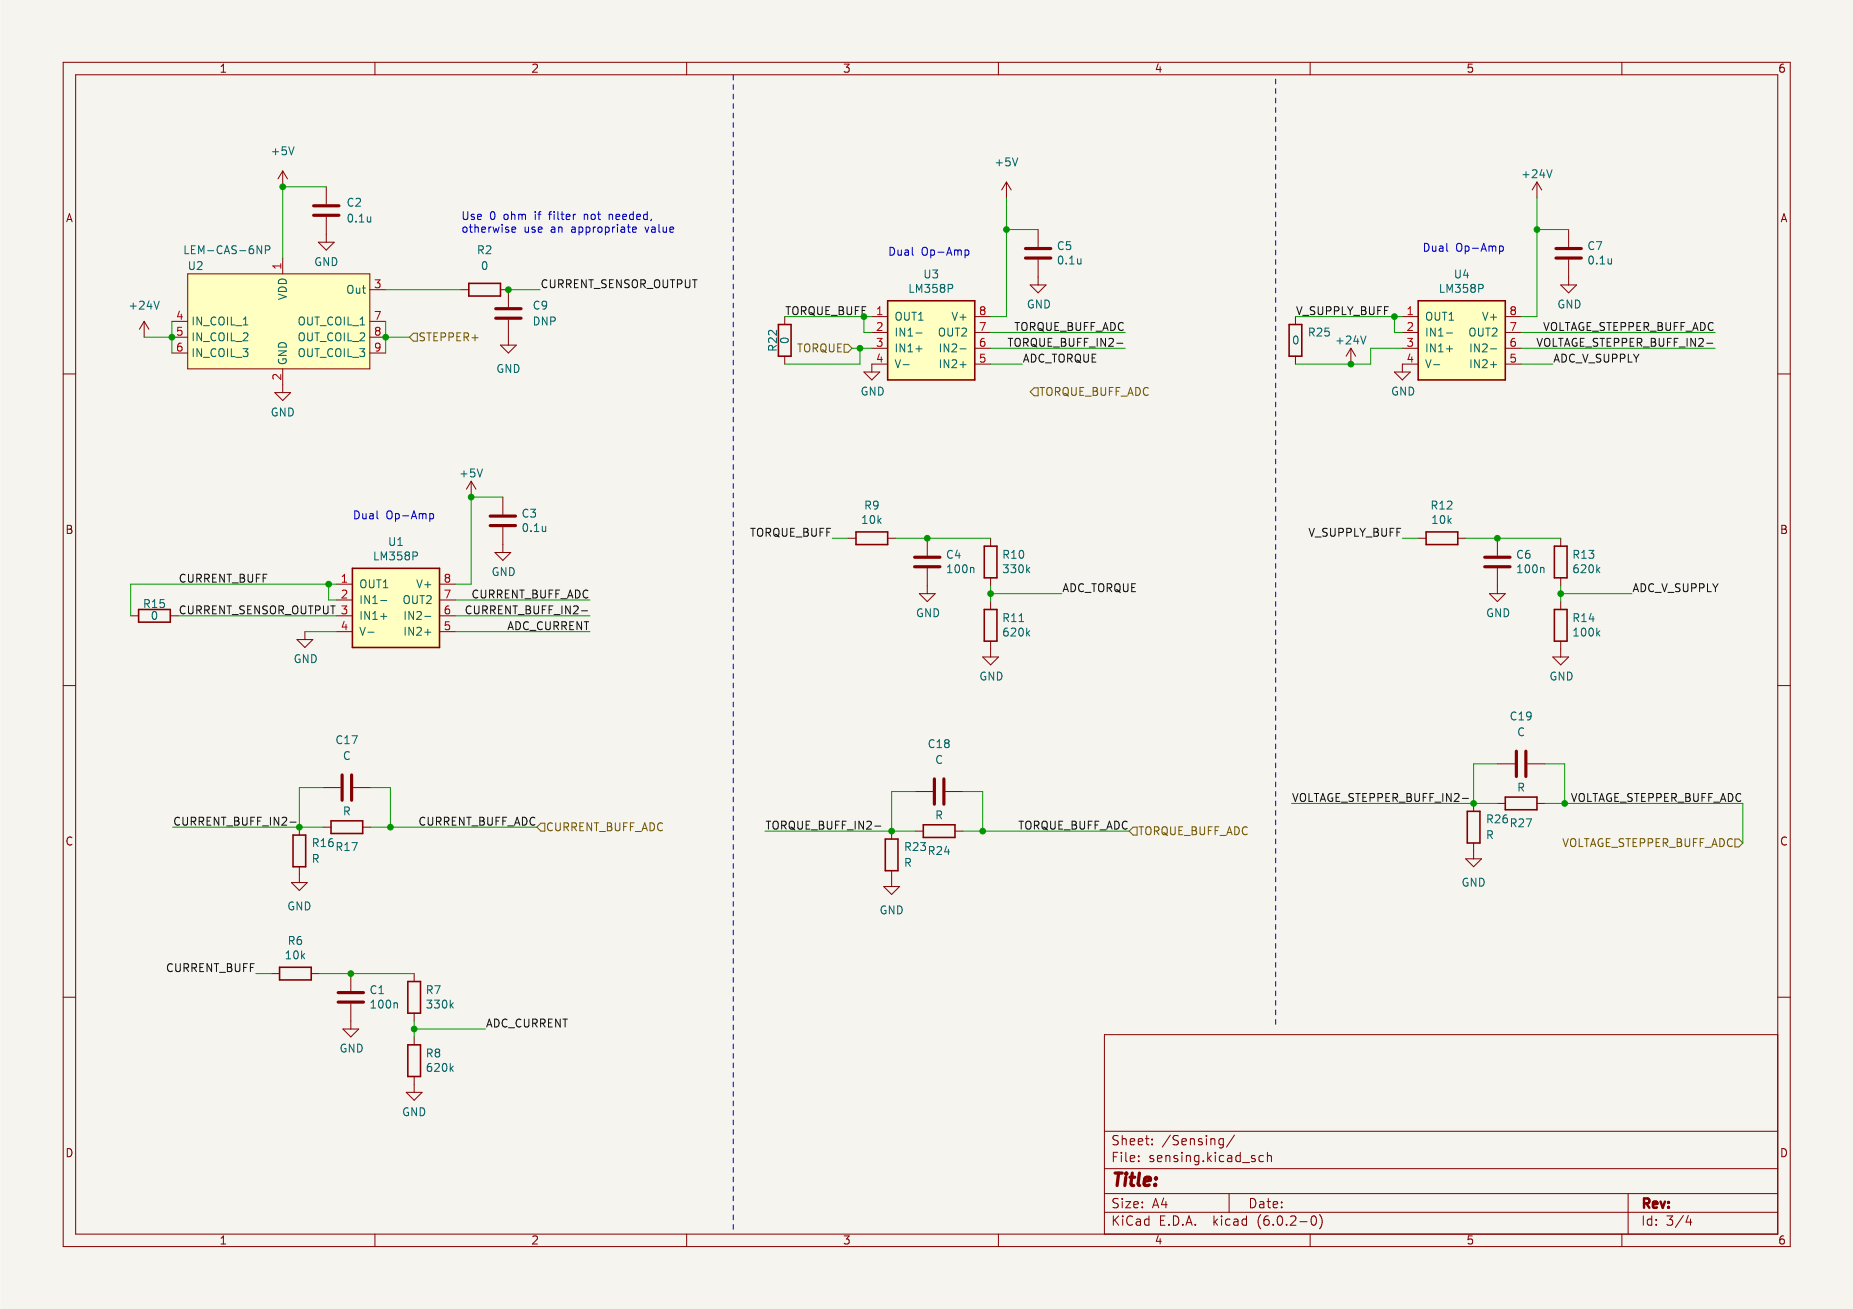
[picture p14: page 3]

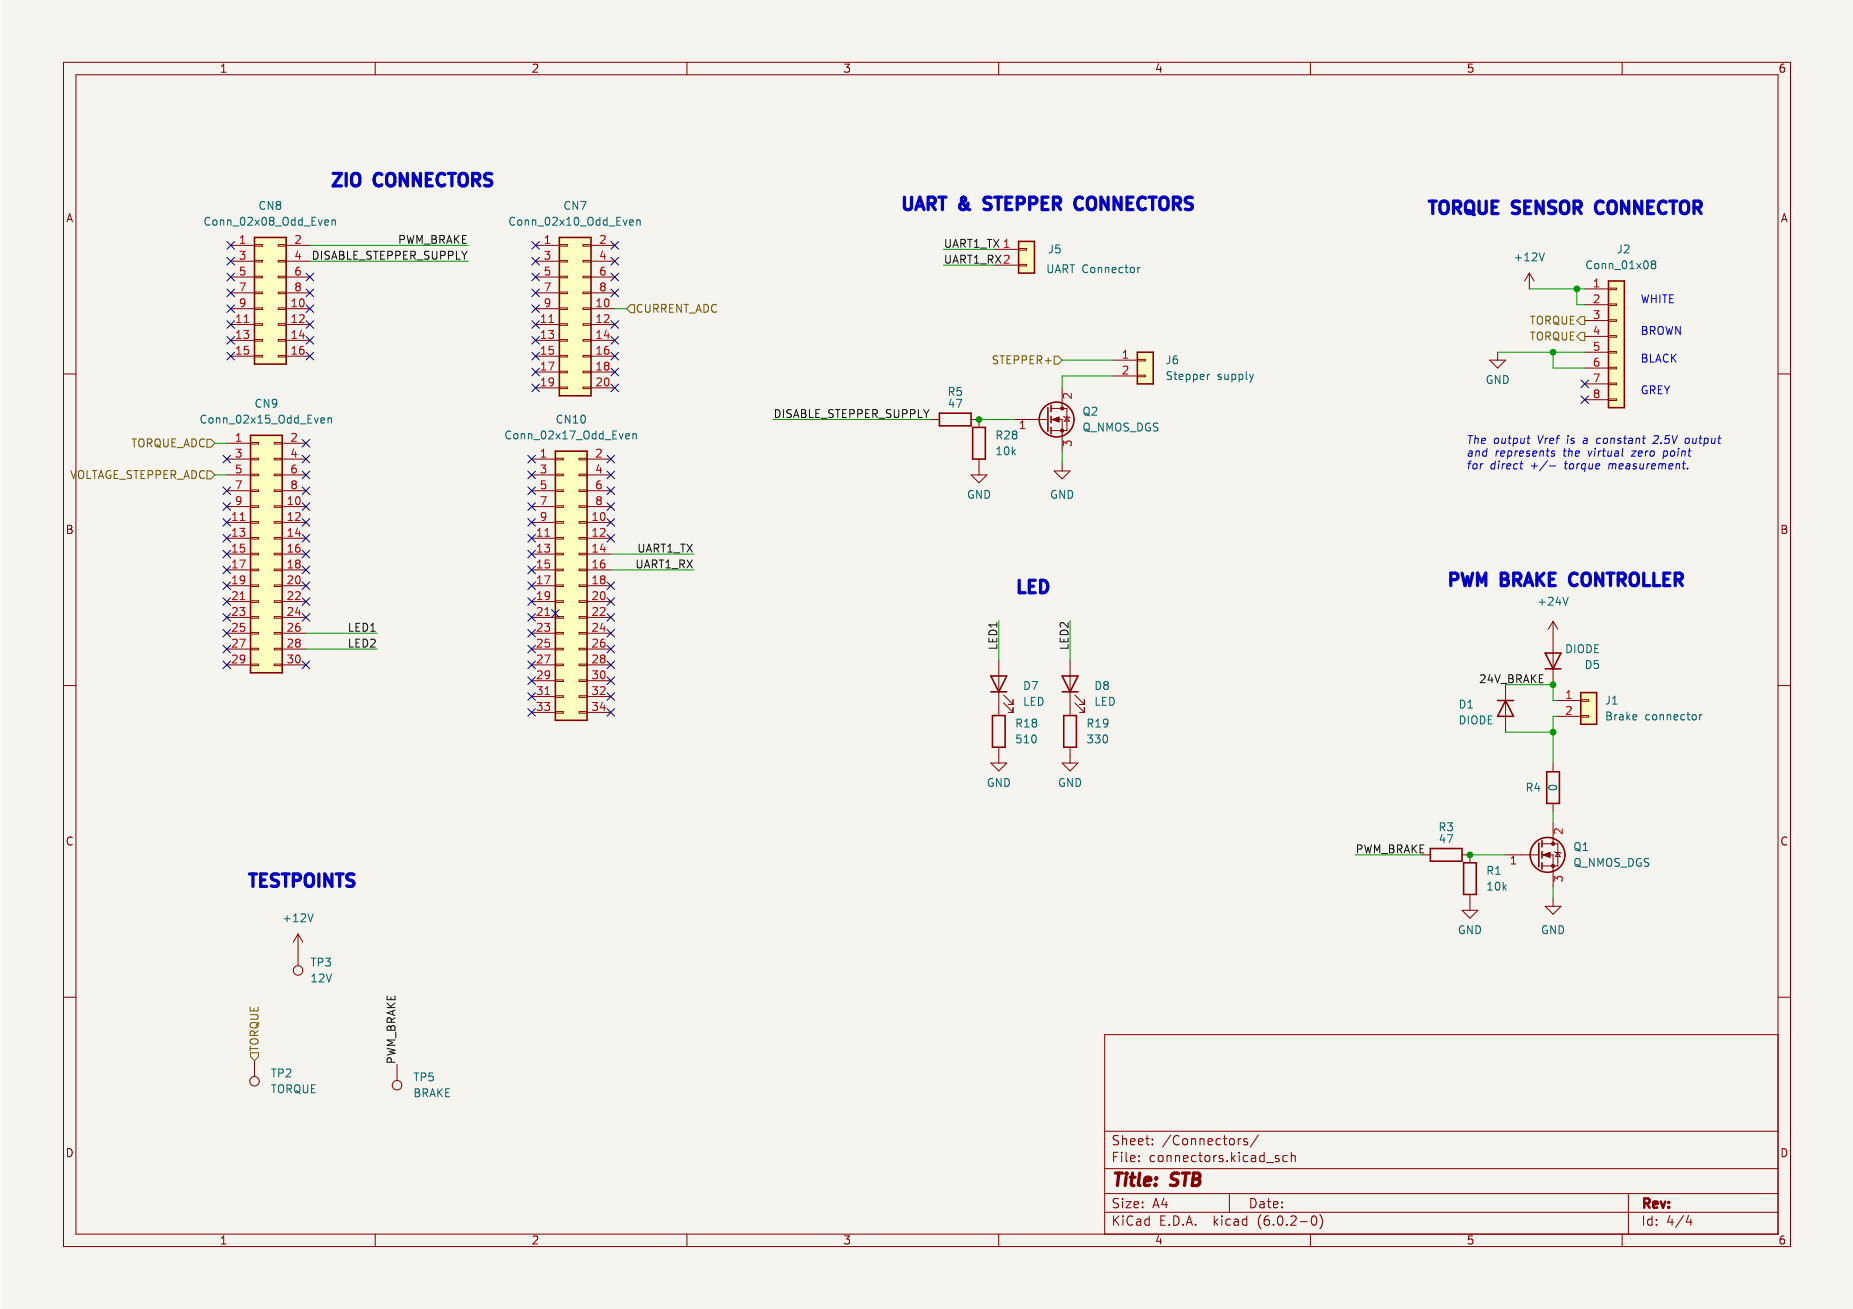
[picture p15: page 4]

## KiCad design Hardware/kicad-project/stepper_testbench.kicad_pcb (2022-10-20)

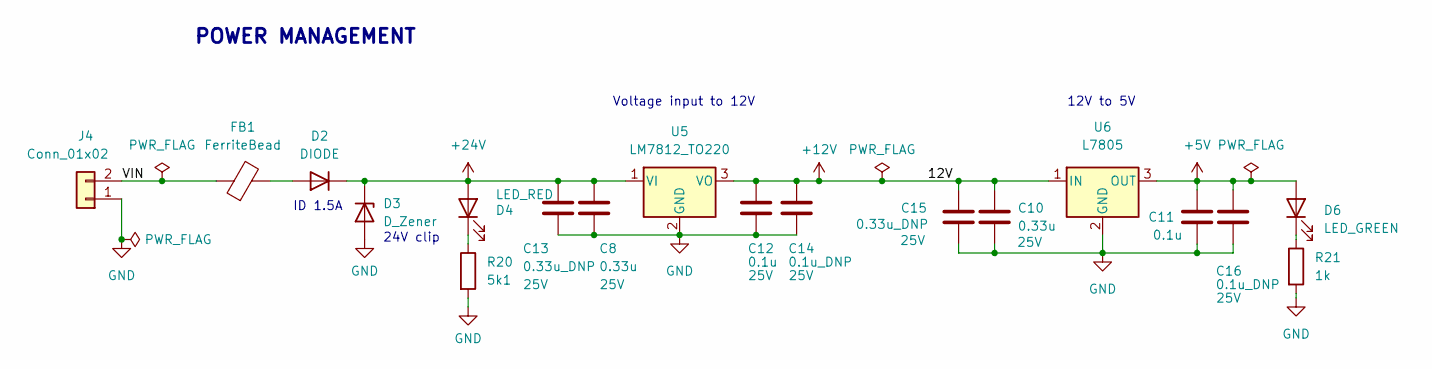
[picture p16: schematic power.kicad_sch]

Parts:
C8, C10: 0.33u; C_0603_1608Metric
C11, C12: 0.1u; C_0603_1608Metric
C13, C15: 0.33u_DNP; CP_Radial_D5.0mm_P2.50mm
C14, C16: 0.1u_DNP; CP_Radial_D5.0mm_P2.50mm
D2: DIODE; D_SOD-323
D3: D_Zener; D_SMA
D4: LED_RED; LED_0603_1608Metric
D6: LED_GREEN; LED_0603_1608Metric
FB1: FerriteBead; R_0805_2012Metric
J4: Conn_01x02; PinHeader_1x02_P2.54mm_Vertical
R20: 5k1; R_0603_1608Metric
R21: 1k; R_0603_1608Metric
U5: LM7812_TO220; TO-220-3_Vertical
U6: L7805; TO-220-3_Vertical

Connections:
+5V: C11.1, C16.1, D6.2 (A), U6.3 (OUT); also elsewhere on the board
+12V: C10.1, C12.1, C14.1, C15.1, U5.3 (VO), U6.1 (IN); also elsewhere on the board
+24V: C8.1, C13.1, D2.2 (K), D3.1 (K), D4.2 (A), U5.1 (VI); also elsewhere on the board
/Power/VIN: FB1.1, J4.2
GND: C8.2, C10.2, C11.2, C12.2, C13.2, C14.2, C15.2, C16.2, D3.2 (A), J4.1, R20.2, R21.2, U5.2 (GND), U6.2 (GND); also elsewhere on the board
unnamed: D2.1 (A), FB1.2
unnamed: D4.1 (K), R20.1
unnamed: D6.1 (K), R21.1

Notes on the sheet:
Voltage input to 12V
POWER MANAGEMENT
24V clip
12V to 5V
ID 1.5A

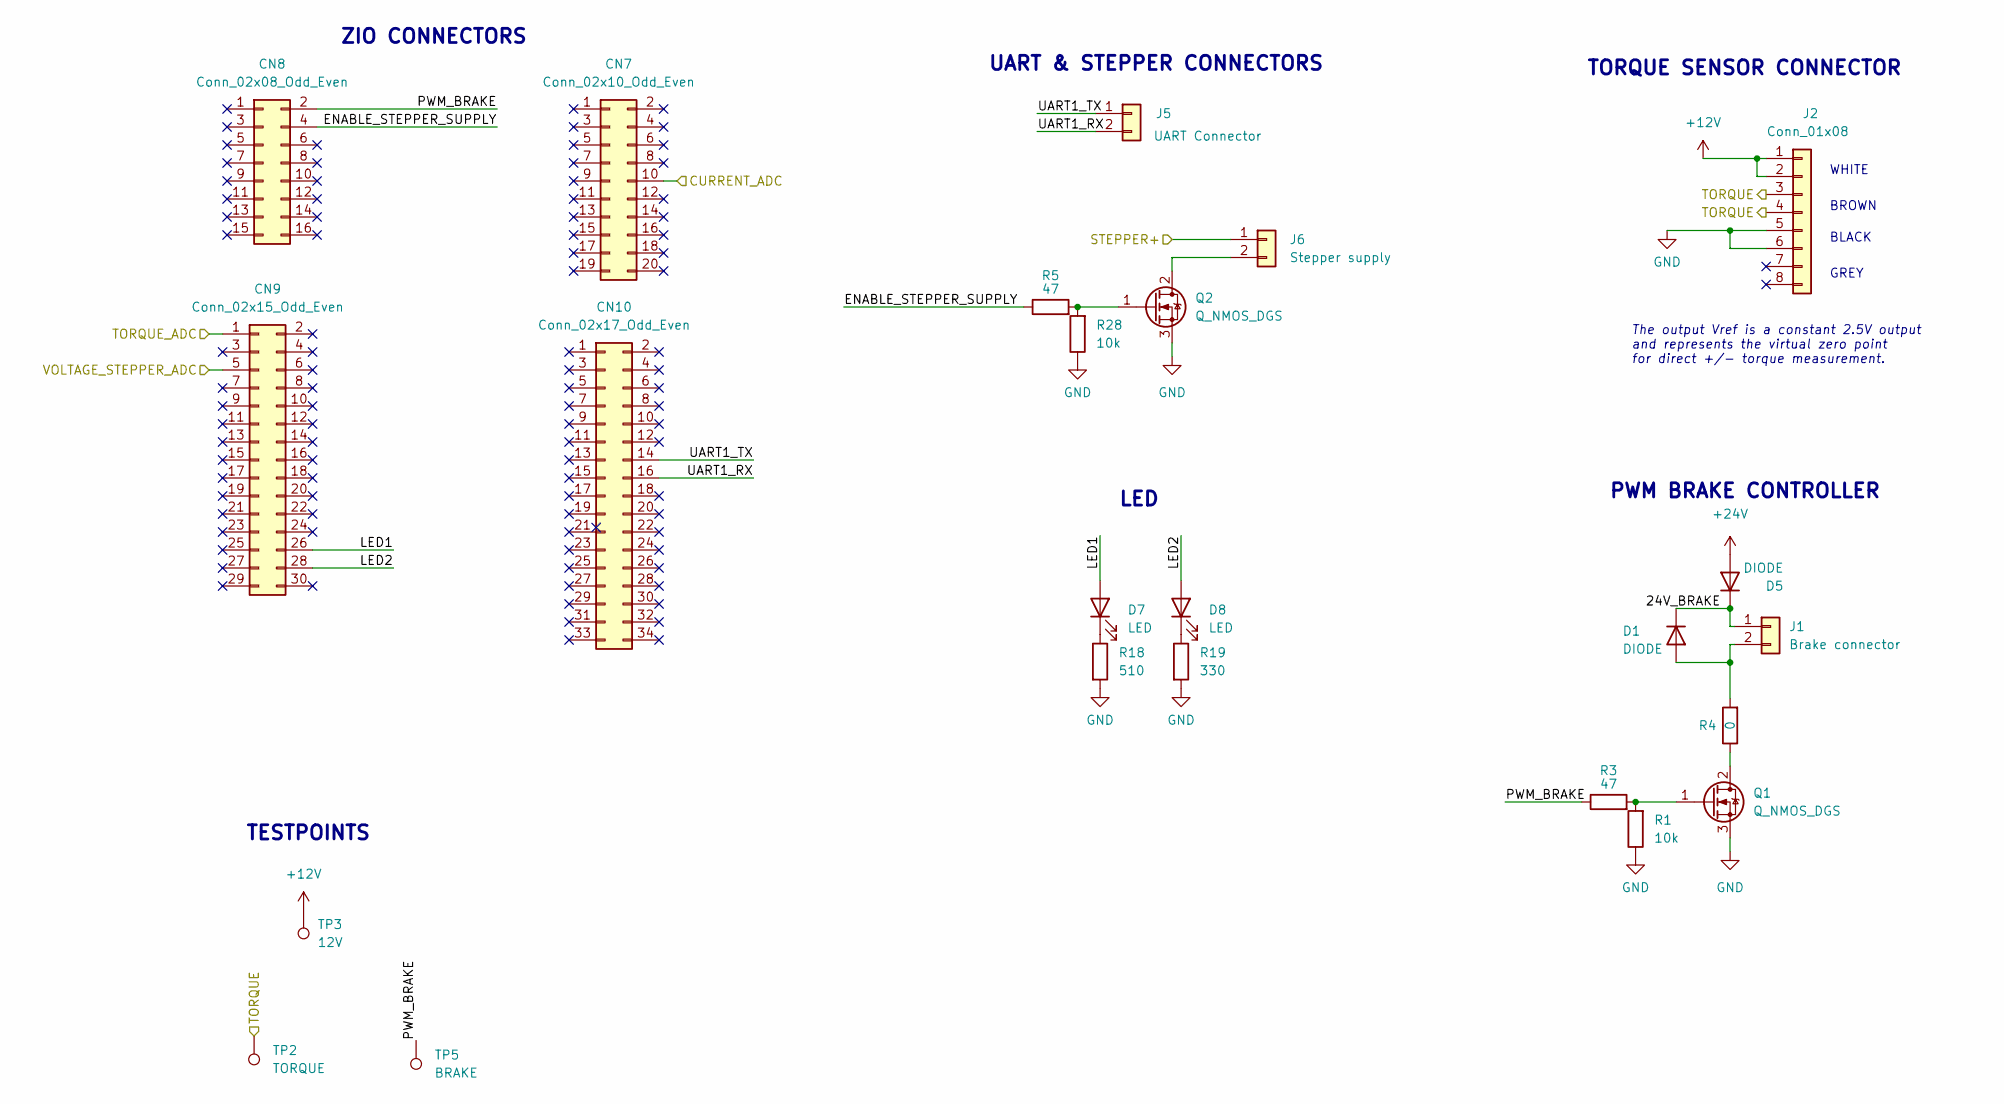
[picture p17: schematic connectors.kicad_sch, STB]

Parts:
CN7: Conn_02x10_Odd_Even; PinHeader_2x10_P2.54mm_Vertical
CN8: Conn_02x08_Odd_Even; PinHeader_2x08_P2.54mm_Vertical
CN9: Conn_02x15_Odd_Even; PinHeader_2x15_P2.54mm_Vertical
CN10: Conn_02x17_Odd_Even; PinHeader_2x17_P2.54mm_Vertical
D1, D5: DIODE; D_SOD-323
D7, D8: LED; LED_0603_1608Metric
J1: Brake connector; PinHeader_1x02_P2.54mm_Vertical
J2: Conn_01x08; PinHeader_1x08_P2.54mm_Vertical
J5: UART Connector; PinHeader_1x02_P2.54mm_Vertical
J6: Stepper supply; PinHeader_1x02_P2.54mm_Vertical
Q1, Q2: Q_NMOS_DGS; TO-252-2
R1, R28: 10k; R_0603_1608Metric
R3, R5: 47; R_0603_1608Metric
R4: 0; R_0603_1608Metric
R18: 510; R_0603_1608Metric
R19: 330; R_0603_1608Metric
TP2: TORQUE; TestPoint_Pad_D2.0mm
TP3: 12V; TestPoint_Pad_D2.0mm
TP5: BRAKE; TestPoint_Pad_D2.0mm

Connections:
+12V: J2.1, J2.2, TP3.1; also elsewhere on the board
+24V: D5.1 (A); also elsewhere on the board
/Connectors/24V_BRAKE: D1.2 (K), D5.2 (K), J1.1
/Connectors/ENABLE_STEPPER_SUPPLY: CN8.4, R5.1
/Connectors/LED1: CN9.26, D7.2 (A)
/Connectors/LED2: CN9.28, D8.2 (A)
/Connectors/PWM_BRAKE: CN8.2, R3.1, TP5.1
/Connectors/STEPPER+: J6.1; also elsewhere on the board
/Connectors/TORQUE: J2.3, J2.4, TP2.1; also elsewhere on the board
/Connectors/UART1_RX: CN10.16, J5.2
/Connectors/UART1_TX: CN10.14, J5.1
/Sensing/CURRENT_BUFF_ADC: CN7.10; also elsewhere on the board
/Sensing/TORQUE_BUFF_ADC: CN9.1; also elsewhere on the board
/Sensing/VOLTAGE_STEPPER_BUFF_ADC: CN9.5; also elsewhere on the board
GND: J2.5, J2.6, Q1.3 (S), Q2.3 (S), R1.1, R18.2, R19.2, R28.1; also elsewhere on the board
unnamed: D1.1 (A), J1.2, R4.2
unnamed: D7.1 (K), R18.1
unnamed: D8.1 (K), R19.1
unnamed: Q1.1 (G), R1.2, R3.2
unnamed: Q1.2 (D), R4.1
unnamed: Q2.1 (G), R5.2, R28.2
unnamed: J6.2, Q2.2 (D)

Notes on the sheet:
LED
TORQUE SENSOR CONNECTOR
BROWN
BLACK
WHITE
GREY
The output Vref is a constant 2.5V output and represents the virtual zero point for direct +/- torque measurement.
UART & STEPPER CONNECTORS
TESTPOINTS
ZIO CONNECTORS
PWM BRAKE CONTROLLER

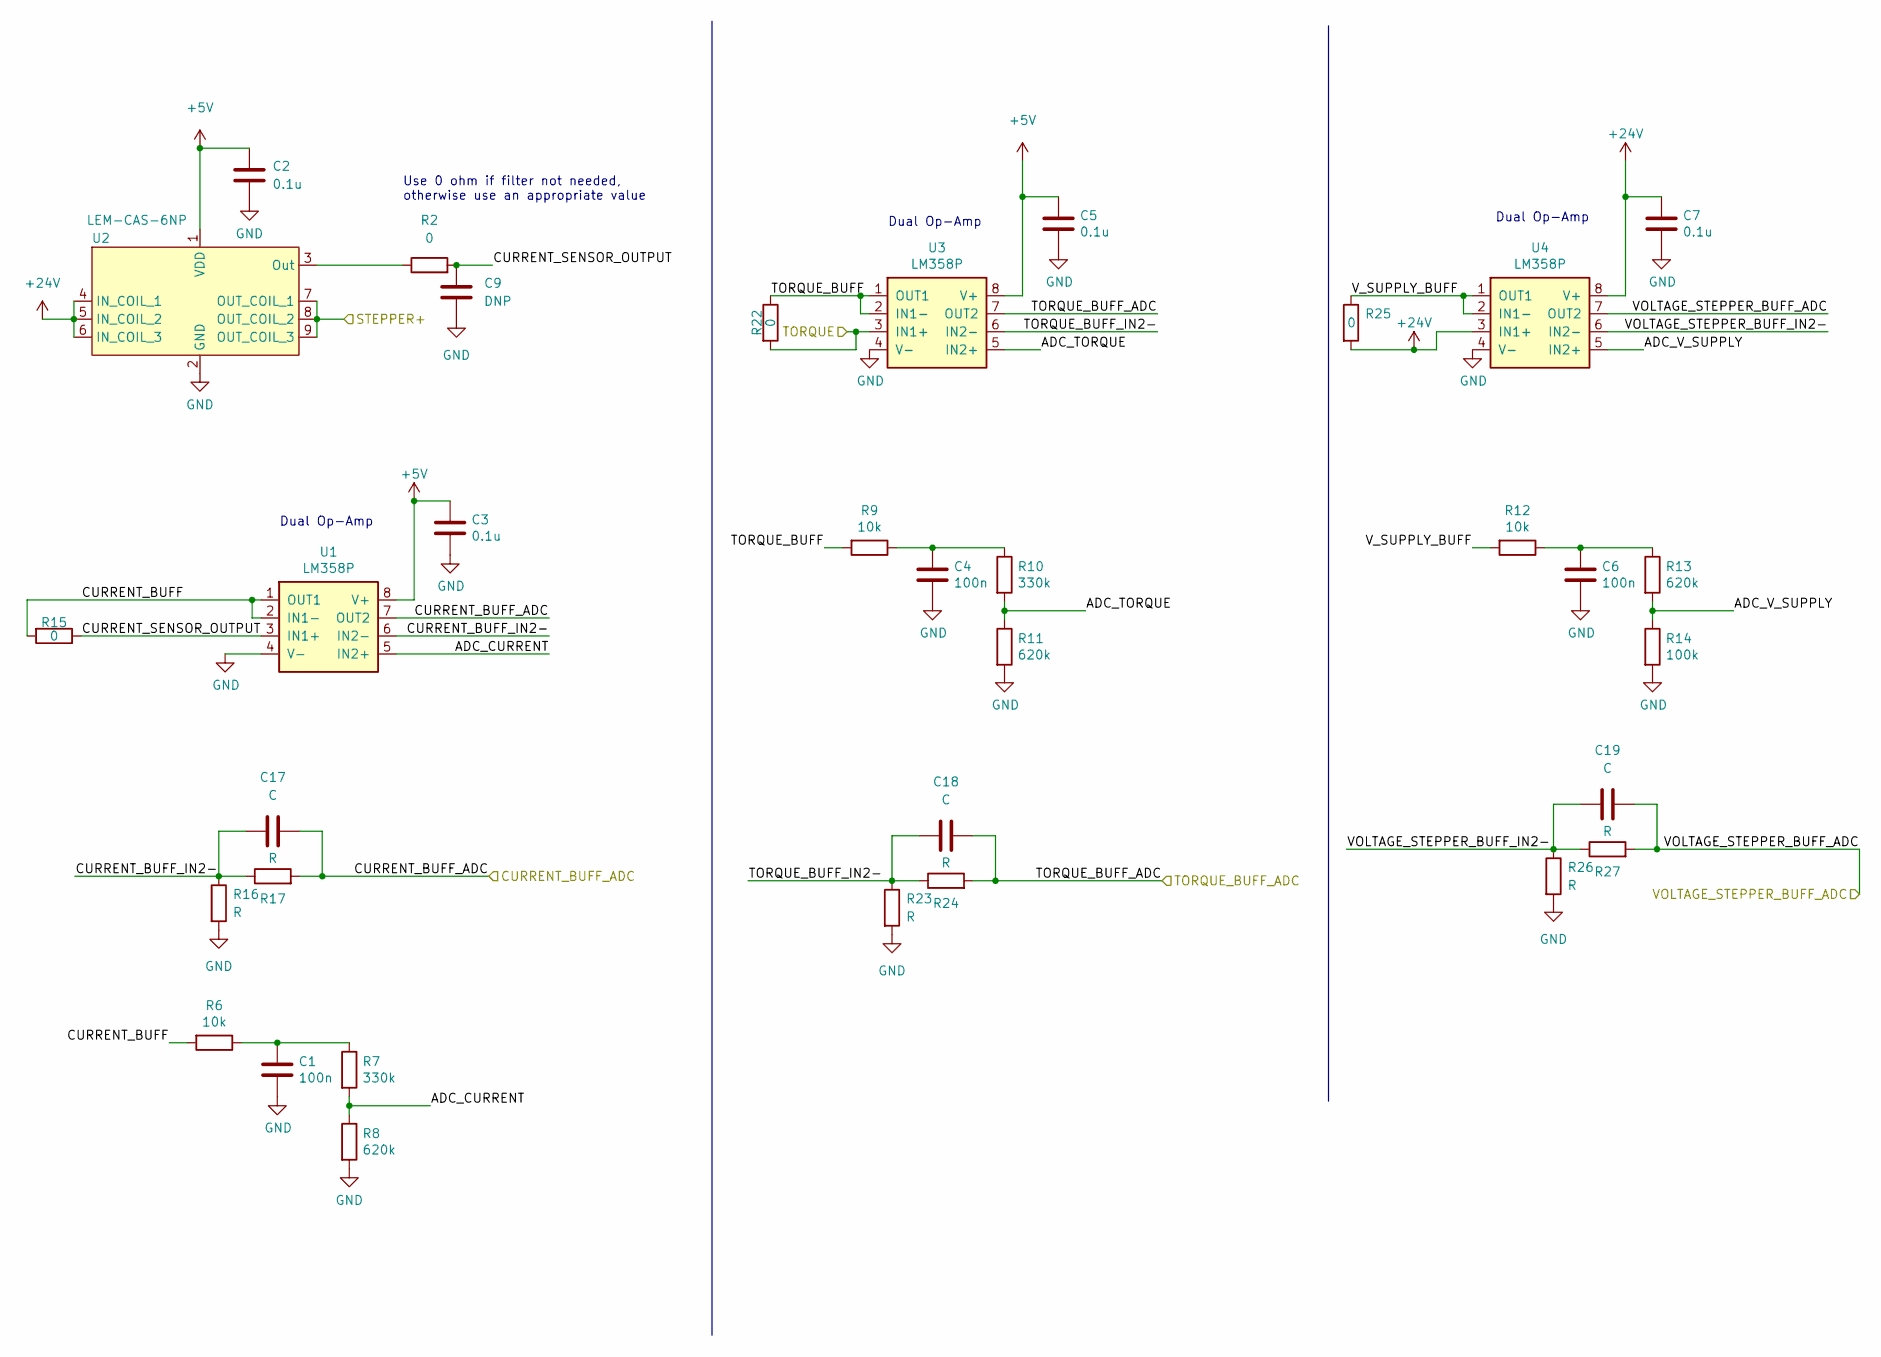
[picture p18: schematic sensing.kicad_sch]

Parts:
C1, C4, C6: 100n; C_0603_1608Metric
C2, C3, C5, C7: 0.1u; C_0603_1608Metric
C9: DNP; C_0805_2012Metric
C17, C18, C19: C; C_0805_2012Metric
R2, R15, R22, R25: 0; R_0603_1608Metric
R6, R9, R12: 10k; R_0603_1608Metric
R7, R10: 330k; R_0603_1608Metric
R8, R11, R13: 620k; R_0603_1608Metric
R14: 100k; R_0603_1608Metric
R16, R17, R23, R24, R26, R27: R; R_0603_1608Metric
U1, U3, U4: LM358P; DIP-8_W7.62mm
U2: LEM-CAS-6NP; LEM-CAS-6-NP

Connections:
+5V: C2.1, C3.1, C5.1, U1.8 (V+), U2.1 (VDD), U3.8 (V+); also elsewhere on the board
+24V: C7.1, R25.2, U2.4 (IN_COIL_1), U2.5 (IN_COIL_2), U2.6 (IN_COIL_3), U4.3 (IN1+), U4.8 (V+); also elsewhere on the board
/Connectors/STEPPER+: U2.7 (OUT_COIL_1), U2.8 (OUT_COIL_2), U2.9 (OUT_COIL_3); also elsewhere on the board
/Connectors/TORQUE: R22.2, U3.3 (IN1+); also elsewhere on the board
/Sensing/ADC_CURRENT: R7.2, R8.1, U1.5 (IN2+)
/Sensing/ADC_TORQUE: R10.2, R11.1, U3.5 (IN2+)
/Sensing/ADC_V_SUPPLY: R13.2, R14.1, U4.5 (IN2+)
/Sensing/CURRENT_BUFF: R6.2, R15.2, U1.1 (OUT1), U1.2 (IN1-)
/Sensing/CURRENT_BUFF_ADC: C17.1, R17.2, U1.7 (OUT2); also elsewhere on the board
/Sensing/CURRENT_BUFF_IN2-: C17.2, R16.1, R17.1, U1.6 (IN2-)
/Sensing/CURRENT_SENSOR_OUTPUT: C9.1, R2.2, R15.1, U1.3 (IN1+)
/Sensing/TORQUE_BUFF: R9.2, R22.1, U3.1 (OUT1), U3.2 (IN1-)
/Sensing/TORQUE_BUFF_ADC: C18.1, R24.2, U3.7 (OUT2); also elsewhere on the board
/Sensing/TORQUE_BUFF_IN2-: C18.2, R23.1, R24.1, U3.6 (IN2-)
/Sensing/VOLTAGE_STEPPER_BUFF_ADC: C19.1, R27.2, U4.7 (OUT2); also elsewhere on the board
/Sensing/VOLTAGE_STEPPER_BUFF_IN2-: C19.2, R26.1, R27.1, U4.6 (IN2-)
/Sensing/V_SUPPLY_BUFF: R12.2, R25.1, U4.1 (OUT1), U4.2 (IN1-)
GND: C1.2, C2.2, C3.2, C4.2, C5.2, C6.2, C7.2, C9.2, R8.2, R11.2, R14.2, R16.2, R23.2, R26.2, U1.4 (V-), U2.2 (GND), U3.4 (V-), U4.4 (V-); also elsewhere on the board
unnamed: C1.1, R6.1, R7.1
unnamed: C4.1, R9.1, R10.1
unnamed: C6.1, R12.1, R13.1
unnamed: R2.1, U2.3 (Out)

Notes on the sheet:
Dual Op-Amp
Use 0 ohm if filter not needed, otherwise use an appropriate value

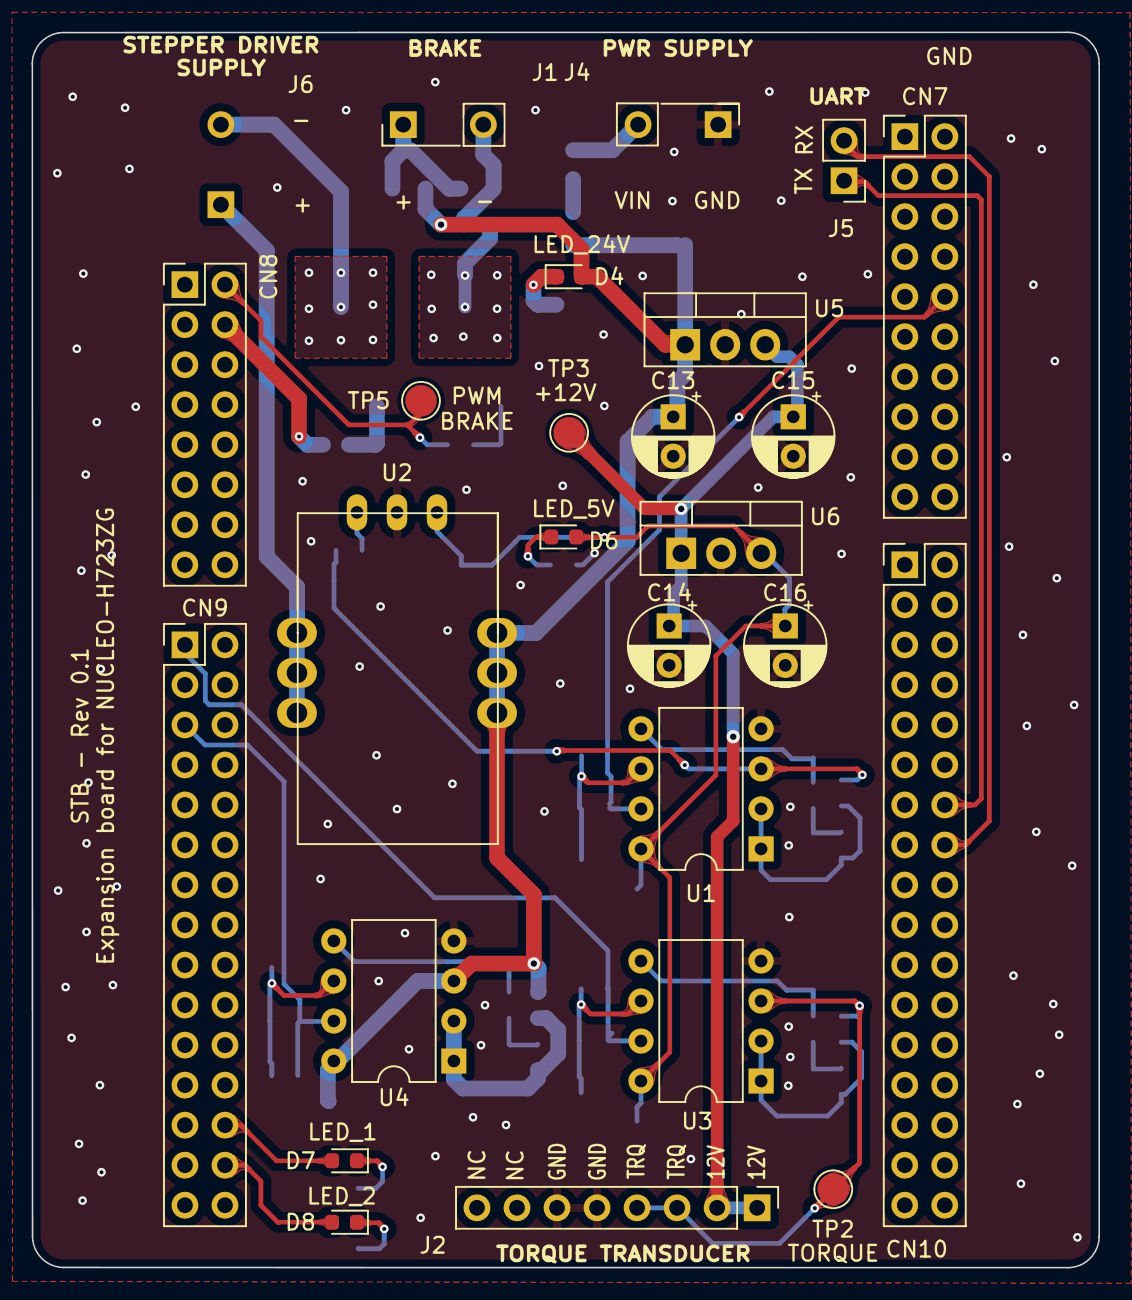
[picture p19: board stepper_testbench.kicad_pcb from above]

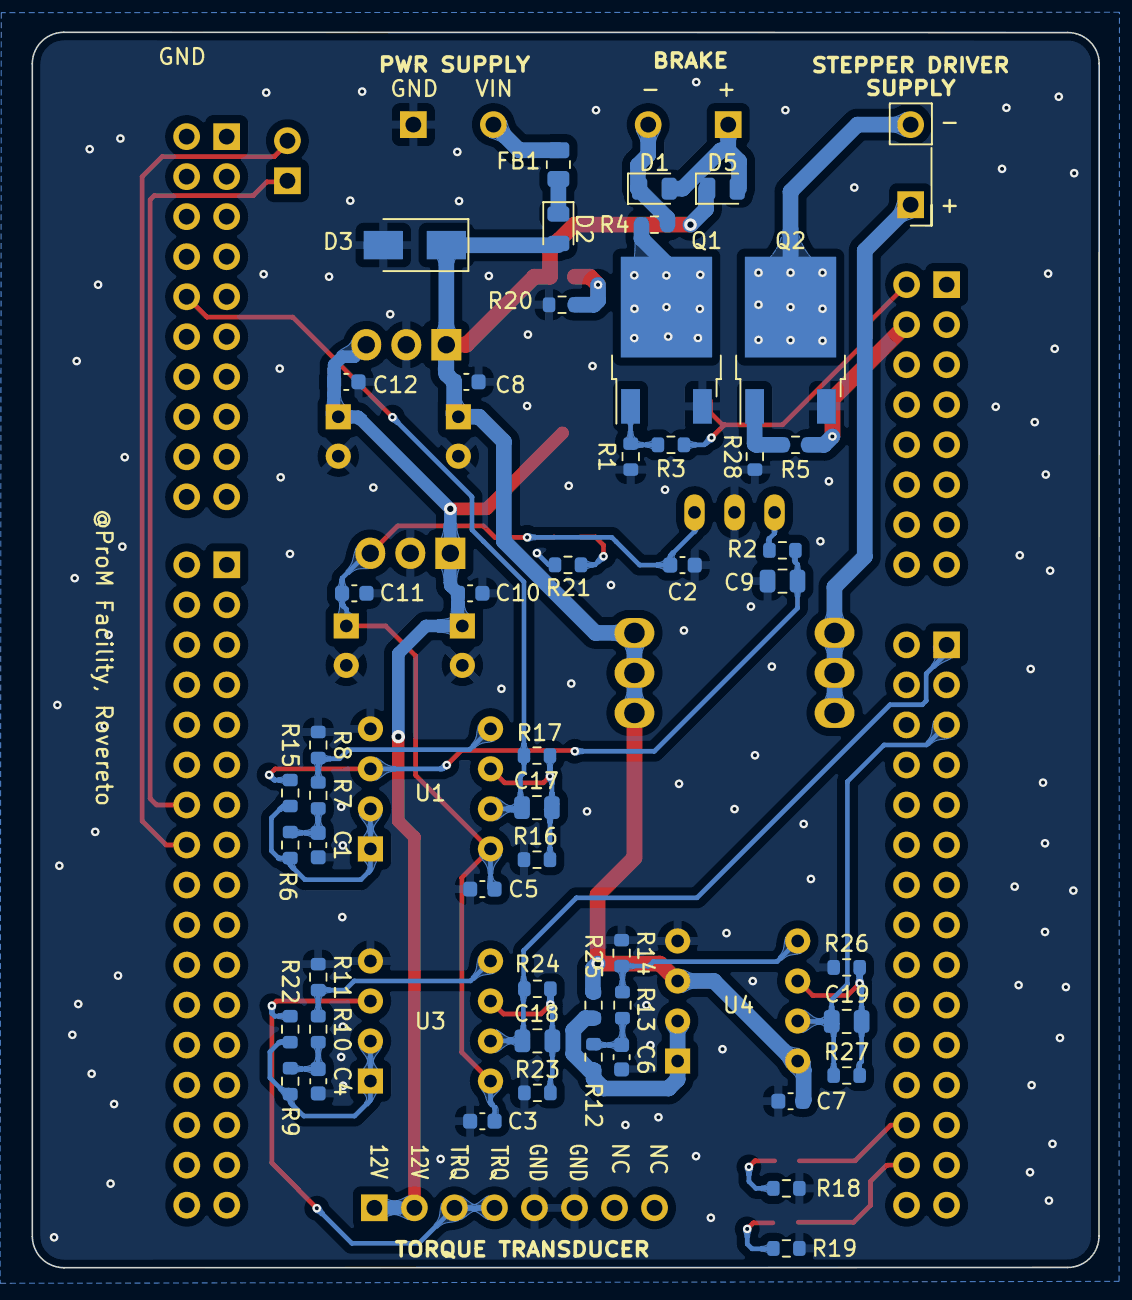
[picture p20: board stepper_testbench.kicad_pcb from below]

Board: 2 copper layers, 67.7 x 78.4 mm, 76 parts (55 on the bottom side), 41 nets.

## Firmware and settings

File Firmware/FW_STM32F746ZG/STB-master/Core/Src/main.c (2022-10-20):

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
/* Includes ------------------------------------------------------------------*/
#include "main.h"

#include "adc.h"
#include "dma.h"
#include "gpio.h"
#include "tim.h"
#include "usart.h"

/* USER CODE BEGIN Includes */
#include "brake.h"
#include "pwm.h"
#include "slave_cmd_utils.h"
#include "timer_utils.h"

#include <stdbool.h>
#include <stdio.h>
#include <stdlib.h>
#include <string.h>
/* USER CODE END Includes */

/* USER CODE BEGIN PD */
#define ACQUISITION_TIME_DIGITS  2
#define CMD_PAYLOAD_LENGHT       100
#define MAX_CMD_SEND_ATTEMPTS    100
#define MAX_ACK_DELAY_ALLOWED_MS 20
#define CMD_CLOSING_CHAR         '\n'
/* USER CODE END PD */


/* USER CODE BEGIN PV */
typedef struct {
    bool is_word_complete;
    char cmd_received[CMD_PAYLOAD_LENGHT];
    char last_char_received;
    uint8_t char_index;
} uart_rx_handler;

uart_rx_handler gui_cmd_handler;
uart_rx_handler slave_cmd_handler;

typedef enum {
    INIT = 0U,
    WAITING_FOR_CMD,
    CMD_RECEIVED,
    SEND_START_MOTOR_CMD,
    GET_MOTOR_ACK_ON_START,
    MOTOR_IS_RUNNING,
    SENSORS_READING,
    ASYNC_SENSOR_READING,
    SEND_STOP_MOTOR_CMD,
    GET_MOTOR_ACK_ON_STOP,
    MOTOR_IS_STOPPED
} master_state;

typedef struct {
    master_state current_state;
    master_state next_state;
    bool go_to_next_state;
} master_state_machine;

master_state_machine msm_handler;

typedef struct {
    bool is_powered;
} stepper_handler;

stepper_handler stepper;
uint8_t sendings_attempts_done = 0;
uint32_t current_tick          = 0;
uint32_t deadline              = 0;
uint8_t gui_acquisition_time   = 0;
char gui_acquisition_time_str[ACQUISITION_TIME_DIGITS];
float brake_single_step_period = 0.0;
bool is_brake_at_max_value     = false;
bool do_async_sensor_reading   = false;
// ADC variables
volatile float torque_gpio;
volatile float board_voltage;
volatile float stepper_current;
char adc_out[100];

//bool is_sampling = false;
/* USER CODE END PV */

void SystemClock_Config(void);
/* USER CODE BEGIN PFP */
void set_and_go_to_next_state(master_state next_state);
bool parse_gui_cmd(char *cmd_rx);
void reset_cmd(uart_rx_handler *uart_handler);
void update_sensor_values();
void update_sensor_values_and_print();
/* USER CODE END PFP */

/**
  * @brief  The application entry point.
  * @retval int
  */
int main(void) {
    /* MCU Configuration--------------------------------------------------------*/

    /* Reset of all peripherals, Initializes the Flash interface and the Systick. */
    HAL_Init();

    /* Configure the system clock */
    SystemClock_Config();

    /* Initialize all configured peripherals */
    MX_GPIO_Init();
    MX_DMA_Init();
    MX_ADC1_Init();
    MX_ADC2_Init();
    MX_ADC3_Init();
    MX_TIM1_Init();
    MX_TIM3_Init();
    MX_USART3_UART_Init();
    MX_USART6_UART_Init();
    MX_TIM2_Init();
    MX_TIM6_Init();
    /* USER CODE BEGIN 2 */
    HAL_GPIO_WritePin(DEBUG_SIGNAL_1_GPIO_Port, DEBUG_SIGNAL_1_Pin, GPIO_PIN_RESET);
    HAL_GPIO_WritePin(DEBUG_SIGNAL_2_GPIO_Port, DEBUG_SIGNAL_2_Pin, GPIO_PIN_RESET);
    HAL_GPIO_WritePin(ENABLE_STEPPER_SUPPLY_GPIO_Port, ENABLE_STEPPER_SUPPLY_Pin, GPIO_PIN_SET);
    // INIT PHASE
    msm_handler.current_state    = INIT;
    msm_handler.next_state       = WAITING_FOR_CMD;
    msm_handler.go_to_next_state = true;
    reset_cmd(&gui_cmd_handler);
    reset_cmd(&slave_cmd_handler);
    stepper.is_powered = false;

    uint32_t sensor_time = 5000;

    //HAL_GPIO_WritePin(ENABLE_STEPPER_SUPPLY_GPIO_Port, ENABLE_STEPPER_SUPPLY_Pin, GPIO_PIN_RESET);
    memset(adc_out, 0x00, sizeof(adc_out));

    brake_init(&magnetic_brake);
    brake_set_pwm_duty_cycle(&magnetic_brake, 0.0);
    brake_on(&magnetic_brake);

    ADC_start_DMA_readings();

    for (int i = 0; i < 10; i++) {
        measured_zero_current_value = ADC_get_current_to_gpio_level();
        measured_zero_torque_value  = ADC_get_torque_to_gpio_level();
    }
    /* USER CODE END 2 */

    /* Infinite loop */
    /* USER CODE BEGIN WHILE */
    while (1) {
        // while (1) {
        // while (1) {
        //     HAL_UART_Receive_IT(&UART_USB, (uint8_t *)&gui_cmd_handler.last_char_received, 1);
        //     if (gui_cmd_handler.is_word_complete) {
        //         parse_gui_cmd(gui_cmd_handler.cmd_received);
        //         reset_cmd(&gui_cmd_handler);
        //     }
        //     if (is_sampling) {
        //         brake_single_step_period = gui_acquisition_time / TOTAL_PWM_BRAKE_STEPS;
        //         brake_set_pwm_duty_cycle(&magnetic_brake, 0.0);
        //         brake_set_and_start_step_timer((uint32_t)brake_single_step_period * 1000);
        //         is_sampling = false;
        //     }
        //     if (magnetic_brake.is_top_limit_reached) {
        //         brake_stop_step_timer();
        //         magnetic_brake.is_top_limit_reached = false;
        //     }
        // }
        //     // update_sensor_values_and_print();
        //     // HAL_Delay(100);
        // }
        /* USER CODE END WHILE */

        /* USER CODE BEGIN 3 */
        // while (1) {
        //     HAL_UART_Receive_IT(&UART_USB, (uint8_t *)&gui_cmd_handler.last_char_received, 1);
        //     if (gui_cmd_handler.is_word_complete) {
        //         parse_gui_cmd(gui_cmd_handler.cmd_received);
        //         reset_cmd(&gui_cmd_handler);
        //     }
        //     if (is_sampling) {
        //         brake_single_step_period = gui_acquisition_time / TOTAL_PWM_BRAKE_STEPS;
        //         brake_set_pwm_duty_cycle(&magnetic_brake, 0.0);
        //         brake_set_and_start_step_timer((uint32_t)brake_single_step_period * 1000);
        //         is_sampling = false;
        //     }
        //     if (magnetic_brake.is_top_limit_reached) {
        //         brake_stop_step_timer();
        //         magnetic_brake.is_top_limit_reached = false;
        //     }
        // }
        //     // update_sensor_values_and_print();
        //     // HAL_Delay(100);
        // }
        /* USER CODE END WHILE */
        if (msm_handler.go_to_next_state) {
            msm_handler.current_state = msm_handler.next_state;
        }
        switch (msm_handler.current_state) {
            case INIT:
                HAL_NVIC_SystemReset();
                break;
            case WAITING_FOR_CMD:
                HAL_GPIO_WritePin(DEBUG_SIGNAL_1_GPIO_Port, DEBUG_SIGNAL_1_Pin, GPIO_PIN_RESET);
                HAL_GPIO_WritePin(DEBUG_SIGNAL_2_GPIO_Port, DEBUG_SIGNAL_2_Pin, GPIO_PIN_SET);
                // Continuous receiving
                HAL_UART_Receive_IT(&UART_USB, (uint8_t *)&gui_cmd_handler.last_char_received, sizeof(char));
                if (gui_cmd_handler.is_word_complete) {
                    set_and_go_to_next_state(CMD_RECEIVED);
                }
                break;
            case CMD_RECEIVED:
                HAL_GPIO_WritePin(DEBUG_SIGNAL_2_GPIO_Port, DEBUG_SIGNAL_2_Pin, GPIO_PIN_SET);
                HAL_GPIO_WritePin(DEBUG_SIGNAL_1_GPIO_Port, DEBUG_SIGNAL_1_Pin, GPIO_PIN_SET);
                if (parse_gui_cmd(gui_cmd_handler.cmd_received)) {
                    HAL_GPIO_WritePin(DEBUG_SIGNAL_2_GPIO_Port, DEBUG_SIGNAL_2_Pin, GPIO_PIN_RESET);
                    if (strstr(gui_cmd_handler.cmd_received, "start_motor+")) {
                        // IDEALLY THE MOTOR RUNS FOREVER
                        set_and_go_to_next_state(SEND_START_MOTOR_CMD);
                    } else if (strcmp(gui_cmd_handler.cmd_received, "get_acquired_data_chunks\r") == 0) {
                        set_and_go_to_next_state(ASYNC_SENSOR_READING);
                    }
                } else {
                    set_and_go_to_next_state(WAITING_FOR_CMD);
                }
                HAL_GPIO_WritePin(DEBUG_SIGNAL_2_GPIO_Port, DEBUG_SIGNAL_2_Pin, GPIO_PIN_RESET);
                HAL_GPIO_WritePin(DEBUG_SIGNAL_1_GPIO_Port, DEBUG_SIGNAL_1_Pin, GPIO_PIN_RESET);
                reset_cmd(&gui_cmd_handler);
                break;
            case ASYNC_SENSOR_READING:
                reset_cmd(&gui_cmd_handler);
                // Continuous receiving and sensor reading
                for (uint8_t i = 0; i < 7; i++) {
                    update_sensor_values_and_print();
                }
                set_and_go_to_next_state(WAITING_FOR_CMD);
                break;
            case SEND_START_MOTOR_CMD:
                HAL_GPIO_WritePin(DEBUG_SIGNAL_2_GPIO_Port, DEBUG_SIGNAL_2_Pin, GPIO_PIN_RESET);
                HAL_GPIO_WritePin(DEBUG_SIGNAL_1_GPIO_Port, DEBUG_SIGNAL_1_Pin, GPIO_PIN_SET);
                if (sendings_attempts_done < MAX_CMD_SEND_ATTEMPTS) {
                    HAL_UART_Transmit(&UART_SLAVE, (uint8_t *)"fw+999999\r\n", sizeof("fw+999999\r\n"), 100);
                    HAL_GPIO_WritePin(DEBUG_SIGNAL_1_GPIO_Port, DEBUG_SIGNAL_1_Pin, GPIO_PIN_RESET);
                    reset_cmd(&slave_cmd_handler);
                    sendings_attempts_done++;
                    set_and_go_to_next_state(GET_MOTOR_ACK_ON_START);
                } else {
                    set_and_go_to_next_state(WAITING_FOR_CMD);
                    sendings_attempts_done = 0;
                }
                break;
            case GET_MOTOR_ACK_ON_START:
                current_tick = HAL_GetTick();
                deadline     = current_tick + MAX_ACK_DELAY_ALLOWED_MS;
                HAL_GPIO_WritePin(DEBUG_SIGNAL_2_GPIO_Port, DEBUG_SIGNAL_2_Pin, GPIO_PIN_SET);
                while (current_tick < deadline) {
                    // set zerto torque value
                    //measured_zero_torque_value = ADC_get_torque_to_gpio_level()*;

                    HAL_UART_Receive_IT(&UART_SLAVE, (uint8_t *)&slave_cmd_handler.last_char_received, sizeof(char));
                    if (slave_cmd_handler.is_word_complete &&
                        strcmp(slave_cmd_handler.cmd_received, "start_ack\r\n") == 0) {
                        reset_cmd(&slave_cmd_handler);
                        reset_cmd(&gui_cmd_handler);
                        set_and_go_to_next_state(MOTOR_IS_RUNNING);
                        HAL_GPIO_WritePin(DEBUG_SIGNAL_2_GPIO_Port, DEBUG_SIGNAL_2_Pin, GPIO_PIN_RESET);
                        current_tick = deadline;
                    } else {
                        current_tick = HAL_GetTick();
                    }
                }
                // If timeout has elapsed
                if (msm_handler.next_state == GET_MOTOR_ACK_ON_START) {
                    set_and_go_to_next_state(SEND_START_MOTOR_CMD);
                }
                break;
            case MOTOR_IS_RUNNING:
                // do stuffs
                set_and_go_to_next_state(SENSORS_READING);
                current_tick = HAL_GetTick();
                // update deadline to acquired time from gui (s) * 1000 in order to obtain ms
                deadline                 = current_tick + gui_acquisition_time * 1000;  // sensor_time;
                brake_single_step_period = ((float)gui_acquisition_time) / TOTAL_PWM_BRAKE_STEPS;
                brake_set_pwm_duty_cycle(&magnetic_brake, 0.0);
                brake_set_and_start_step_timer((uint32_t)(brake_single_step_period * 1000));
                break;

            case SENSORS_READING:
                while (!magnetic_brake.is_top_limit_reached) {
                    update_sensor_values_and_print();
                }
                brake_stop_step_timer();
                brake_set_pwm_duty_cycle(&magnetic_brake, 0.0);
                magnetic_brake.is_top_limit_reached = false;

                // while (current_tick < deadline) {
                //     update_sensor_values_and_print();
                //     current_tick = HAL_GetTick();
                // }
                // do stuffs
                set_and_go_to_next_state(SEND_STOP_MOTOR_CMD);
                break;
            case SEND_STOP_MOTOR_CMD:
                HAL_GPIO_WritePin(DEBUG_SIGNAL_2_GPIO_Port, DEBUG_SIGNAL_2_Pin, GPIO_PIN_RESET);
                HAL_GPIO_WritePin(DEBUG_SIGNAL_1_GPIO_Port, DEBUG_SIGNAL_1_Pin, GPIO_PIN_SET);
                if (sendings_attempts_done < MAX_CMD_SEND_ATTEMPTS) {
                    HAL_UART_Transmit(&UART_SLAVE, (uint8_t *)MOTOR_STOP_FOREVER, sizeof(MOTOR_STOP_FOREVER), 100);
                    HAL_GPIO_WritePin(DEBUG_SIGNAL_1_GPIO_Port, DEBUG_SIGNAL_1_Pin, GPIO_PIN_RESET);
                    reset_cmd(&slave_cmd_handler);
                    sendings_attempts_done++;
                    set_and_go_to_next_state(GET_MOTOR_ACK_ON_STOP);
                } else {
                    set_and_go_to_next_state(WAITING_FOR_CMD);
                }
                break;
            case GET_MOTOR_ACK_ON_STOP:

                current_tick = HAL_GetTick();
                deadline     = current_tick + MAX_ACK_DELAY_ALLOWED_MS;
                HAL_GPIO_WritePin(DEBUG_SIGNAL_2_GPIO_Port, DEBUG_SIGNAL_2_Pin, GPIO_PIN_SET);
                while (current_tick < deadline) {
                    HAL_UART_Receive_IT(&UART_SLAVE, (uint8_t *)&slave_cmd_handler.last_char_received, sizeof(char));
                    if (slave_cmd_handler.is_word_complete &&
                        strcmp(slave_cmd_handler.cmd_received, "stop_ack\r\n") == 0) {
                        reset_cmd(&slave_cmd_handler);
                        reset_cmd(&gui_cmd_handler);
                        set_and_go_to_next_state(MOTOR_IS_STOPPED);
                        HAL_GPIO_WritePin(DEBUG_SIGNAL_2_GPIO_Port, DEBUG_SIGNAL_2_Pin, GPIO_PIN_RESET);
                        current_tick = deadline;
                    } else {
                        current_tick = HAL_GetTick();
                    }
                }
                // If timeout has elapsed
                if (msm_handler.next_state == GET_MOTOR_ACK_ON_STOP) {
                    set_and_go_to_next_state(SEND_STOP_MOTOR_CMD);
                }
                break;
            case MOTOR_IS_STOPPED:
                //turn off transistor
                HAL_Delay(2000);
                set_and_go_to_next_state(WAITING_FOR_CMD);
                break;
        }
    }
    /* USER CODE END 3 */
}

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
/* USER CODE BEGIN 4 */
void HAL_UART_RxCpltCallback(UART_HandleTypeDef *huart) {
    if (huart->Instance == UART_USB.Instance) {
        gui_cmd_handler.cmd_received[gui_cmd_handler.char_index] = gui_cmd_handler.last_char_received;
        gui_cmd_handler.char_index++;
        if (gui_cmd_handler.last_char_received == '\r') {
            gui_cmd_handler.is_word_complete = true;
        }
    } else if (huart->Instance == UART_SLAVE.Instance) {
        slave_cmd_handler.cmd_received[slave_cmd_handler.char_index] = slave_cmd_handler.last_char_received;
        slave_cmd_handler.char_index++;
        if (slave_cmd_handler.last_char_received == '\n') {
            slave_cmd_handler.is_word_complete = true;
        }
    }
}

void set_and_go_to_next_state(master_state next_state) {
    msm_handler.next_state       = next_state;
    msm_handler.go_to_next_state = true;
}

void reset_cmd(uart_rx_handler *uart_handler) {
    uart_handler->char_index = 0;
    memset(uart_handler->cmd_received, 0x0, sizeof(uart_handler->cmd_received));
    uart_handler->is_word_complete = false;
}
void send_brake_value_to_gui() {
    char gui_output[15];
    uint8_t len = 0;
    memset(gui_output, 0x00, sizeof(gui_output));
    len = sprintf(gui_output, "PWM+%.2f\r\n", magnetic_brake.pwm_duty_cycle);
    HAL_UART_Transmit(&UART_USB, (uint8_t *)gui_output, len, 100);
}
bool parse_gui_cmd(char *cmd_rx) {
    bool cmd_is_valid = true;
    if (strcmp(cmd_rx, "brake+\r") == 0) {
        if (!magnetic_brake.is_braking) {
            brake_on(&magnetic_brake);
        }
        brake_increase_duty(&magnetic_brake, BRAKE_STEP);
        send_brake_value_to_gui();
    } else if (strcmp(cmd_rx, "brake-\r") == 0) {
        if (!magnetic_brake.is_braking) {
            brake_on(&magnetic_brake);
        }
        brake_decrease_duty(&magnetic_brake, BRAKE_STEP);
        send_brake_value_to_gui();
    } else if (strcmp(cmd_rx, "brake_off\r") == 0) {
        brake_set_pwm_duty_cycle(&magnetic_brake, MIN_ALLOWED_PWM_DUTY);
        brake_off(&magnetic_brake);
        send_brake_value_to_gui();
    } else if (strcmp(cmd_rx, "brake_on_max\r") == 0) {
        brake_set_pwm_duty_cycle(&magnetic_brake, MAX_ALLOWED_PWM_DUTY);
        brake_on(&magnetic_brake);
        send_brake_value_to_gui();
    }
    // else if (strcmp(cmd_rx, "start_motor\r") == 0) {
    //     uint8_t x = 0;
    else if (strstr(cmd_rx, "start_motor+")) {
        // check whether the substring start_motor has been received
        strncpy(gui_acquisition_time_str, &cmd_rx[strlen("start_motor+")], ACQUISITION_TIME_DIGITS);
        gui_acquisition_time = atoi(gui_acquisition_time_str);
        uint8_t x            = 0;
        //is_sampling          = true;
    } else if (strcmp(cmd_rx, "get_acquired_data_chunks\r") == 0) {
        do_async_sensor_reading = true;
    }
    // else if (strcmp(cmd_rx, "stop_async_reading\r") == 0) {
    //     do_async_sensor_reading = false;
    // }
    else {
        cmd_is_valid = false;
    }
    return cmd_is_valid;
}

void HAL_GPIO_EXTI_Callback(uint16_t pin) {
    if (pin == USER_Btn_Pin) {
        (stepper.is_powered)
            ? HAL_GPIO_WritePin(ENABLE_STEPPER_SUPPLY_GPIO_Port, ENABLE_STEPPER_SUPPLY_Pin, GPIO_PIN_RESET)
            : HAL_GPIO_WritePin(ENABLE_STEPPER_SUPPLY_GPIO_Port, ENABLE_STEPPER_SUPPLY_Pin, GPIO_PIN_SET);
        stepper.is_powered = !stepper.is_powered;
    }
}

void update_sensor_values() {
    torque_gpio     = ADC_get_voltage_to_gpio_level();
    board_voltage   = ADC_get_voltage_converted();
    stepper_current = ADC_get_current_converted();
}

void update_sensor_values_and_print() {
    torque_gpio     = ADC_get_torque_converted();   // ADC_get_torque_to_gpio_level();
    board_voltage   = ADC_get_voltage_converted();  // ADC_get_voltage_to_gpio_level();
    stepper_current = ADC_get_current_converted();  // ADC_get_current_to_gpio_level();
#define MEASUREMENT_PRINT 1
#ifdef DEBUG_PRINT
    sprintf(
        adc_out, "Current: %.4f A | STB supply: %.4f V | Trq: %.4f \r\n", stepper_current, board_voltage, torque_gpio);
#endif
#ifdef MEASUREMENT_PRINT
    sprintf(
        adc_out,
        "[MASTER],%lu,%.4f, %.4f,%.4f, %.2f\r\n",
        HAL_GetTick() / 10,
        torque_gpio,
        board_voltage,
        stepper_current,
        magnetic_brake.pwm_duty_cycle * 100);
#endif
    HAL_UART_Transmit(&UART_USB, (uint8_t *)adc_out, sizeof(adc_out), 100);
}
/* USER CODE END 4 */
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


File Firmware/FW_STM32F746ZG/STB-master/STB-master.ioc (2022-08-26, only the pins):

Mcu.UserName=STM32F746ZGTx
PA13.GPIO_Label=TMS
PA13.Signal=SYS_JTMS-SWDIO
PA14.GPIO_Label=TCK
PA14.Signal=SYS_JTCK-SWCLK
PA3.GPIO_Label=TORQUE_ADC
PA3.Signal=ADCx_IN3
PA5.GPIO_Label=CURRENT_ADC
PA5.Signal=ADCx_IN5
PB0.GPIO_Label=LD1 [Green]
PB0.Signal=GPIO_Output
PB10.GPIO_Label=DEBUG_PIN_5
PB10.Signal=GPIO_Output
PB11.GPIO_Label=DEBUG_PIN_4
PB11.Signal=GPIO_Output
PB14.GPIO_Label=LD3 [Red]
PB14.Signal=GPIO_Output
PB3.GPIO_Label=SW0
PB3.Signal=SYS_JTDO-SWO
PB7.GPIO_Label=LD2 [Blue]
PB7.Signal=GPIO_Output
PC13.GPIO_Label=USER_Btn [B1]
PC13.Signal=GPXTI13
PC14/OSC32_IN.Signal=RCC_OSC32_IN
PC15/OSC32_OUT.Signal=RCC_OSC32_OUT
PC3.GPIO_Label=STEPPER_VOLTAGE_ADC
PC3.Signal=ADCx_IN13
PC8.GPIO_Label=PWM_BRAKE
PC8.Signal=S_TIM3_CH3
PC9.GPIO_Label=ENABLE_STEPPER_SUPPLY
PC9.Signal=GPIO_Output
PD0.GPIO_Label=DEBUG_SIGNAL_1
PD0.Signal=GPIO_Output
PD8.GPIO_Label=STLK_RX [STM32F103CBT6_PA3]
PD8.Signal=USART3_TX
PD9.GPIO_Label=STLK_TX [STM32F103CBT6_PA2]
PD9.Signal=USART3_RX
PE0.GPIO_Label=DEBUG_PIN_3
PE0.Signal=GPIO_Output
PF7.GPIO_Label=LED1
PF7.Signal=GPIO_Output
PF9.GPIO_Label=LED2
PF9.Signal=GPIO_Output
PG0.GPIO_Label=DEBUG_SIGNAL_2
PG0.Signal=GPIO_Output
PG14.Signal=USART6_TX
PG6.GPIO_Label=USB_PowerSwitchOn [STMPS2151STR_EN]
PG6.Signal=GPIO_Output
PG7.GPIO_Label=USB_OverCurrent [STMPS2151STR_FAULT]
PG7.Signal=GPIO_Input
PG9.Signal=USART6_RX
PH0/OSC_IN.GPIO_Label=MCO [STM32F103CBT6_PA8]
PH0/OSC_IN.Signal=RCC_OSC_IN
PH1/OSC_OUT.Signal=RCC_OSC_OUT

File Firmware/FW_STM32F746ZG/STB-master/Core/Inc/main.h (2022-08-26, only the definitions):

#define USER_Btn_Pin GPIO_PIN_13
#define USER_Btn_GPIO_Port GPIOC
#define LED1_Pin GPIO_PIN_7
#define LED1_GPIO_Port GPIOF
#define LED2_Pin GPIO_PIN_9
#define LED2_GPIO_Port GPIOF
#define MCO_Pin GPIO_PIN_0
#define MCO_GPIO_Port GPIOH
#define STEPPER_VOLTAGE_ADC_Pin GPIO_PIN_3
#define STEPPER_VOLTAGE_ADC_GPIO_Port GPIOC
#define TORQUE_ADC_Pin GPIO_PIN_3
#define TORQUE_ADC_GPIO_Port GPIOA
#define CURRENT_ADC_Pin GPIO_PIN_5
#define CURRENT_ADC_GPIO_Port GPIOA
#define LD1_Pin GPIO_PIN_0
#define LD1_GPIO_Port GPIOB
#define DEBUG_SIGNAL_2_Pin GPIO_PIN_0
#define DEBUG_SIGNAL_2_GPIO_Port GPIOG
#define DEBUG_PIN_5_Pin GPIO_PIN_10
#define DEBUG_PIN_5_GPIO_Port GPIOB
#define DEBUG_PIN_4_Pin GPIO_PIN_11
#define DEBUG_PIN_4_GPIO_Port GPIOB
#define LD3_Pin GPIO_PIN_14
#define LD3_GPIO_Port GPIOB
#define STLK_RX_Pin GPIO_PIN_8
#define STLK_RX_GPIO_Port GPIOD
#define STLK_TX_Pin GPIO_PIN_9
#define STLK_TX_GPIO_Port GPIOD
#define USB_PowerSwitchOn_Pin GPIO_PIN_6
#define USB_PowerSwitchOn_GPIO_Port GPIOG
#define USB_OverCurrent_Pin GPIO_PIN_7
#define USB_OverCurrent_GPIO_Port GPIOG
#define PWM_BRAKE_Pin GPIO_PIN_8
#define PWM_BRAKE_GPIO_Port GPIOC
#define ENABLE_STEPPER_SUPPLY_Pin GPIO_PIN_9
#define ENABLE_STEPPER_SUPPLY_GPIO_Port GPIOC
#define TMS_Pin GPIO_PIN_13
#define TMS_GPIO_Port GPIOA
#define TCK_Pin GPIO_PIN_14
#define TCK_GPIO_Port GPIOA
#define DEBUG_SIGNAL_1_Pin GPIO_PIN_0
#define DEBUG_SIGNAL_1_GPIO_Port GPIOD
#define SW0_Pin GPIO_PIN_3
#define SW0_GPIO_Port GPIOB
#define LD2_Pin GPIO_PIN_7
#define LD2_GPIO_Port GPIOB
#define DEBUG_PIN_3_Pin GPIO_PIN_0
#define DEBUG_PIN_3_GPIO_Port GPIOE
#define UART_USB                          huart3
#define UART_SLAVE                        huart6
#define TIMER_BRAKE_PWM                   htim3
#define TIMER_BRAKE_PWM_CHANNEL           TIM_CHANNEL_3
#define TIMER_ADC_TRIGGER_CONVERSIONS     htim1
#define TIMER_ADC_CHANNEL_CURRENT_TRIGGER TIM_CHANNEL_1
#define TIMER_ADC_CHANNEL_TORQUE_TRIGGER  TIM_CHANNEL_2
#define TIMER_ADC_CHANNEL_VOLTAGE_TRIGGER TIM_CHANNEL_3
#define TIMER_BRAKE_STEP_CONTROL          htim6
#define ADC_CURRENT                       hadc2
#define ADC_TORQUE                        hadc1
#define ADC_VOLTAGE                       hadc3
#define DMA_CURRENT                       hdma_adc1
#define DMA_TORQUE                        hdma_adc2
#define DMA_VOLTAGE                       hdma_adc3
#define MAX_STEPPER_SUPPLY 24

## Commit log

2021-12-09 features: basic dashboard with save option
    [motor_params.json]
2021-12-10 fix: typos
    [motor_params.json]
2021-12-10 plot: adding more window
    [motor_params.json]
2021-12-12 r/w: implemented r/w with different files
    [motor_params.json]
2021-12-13 fix: missing radio button read & errors handling
    [main.py]
2022-03-18 Moved python code to GUI folder
    [motor_params.json]
2022-03-18 Deleted src folder
    [motor_params.json]
2022-03-22 Moved fw board into FW_STM32F4 folder
2022-07-22 add kicad project
    [calcolo partitori.xlsx, connectors.kicad_sch, sensing.kicad_sch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]
2022-07-23 hw: schematic update
    [connectors.kicad_sch, power.kicad_sch, sensing.kicad_sch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]
2022-07-25 fw: add led state pin to ioc
    [calcolo partitori.xlsx, stepper_testbench.kicad_pcb]
2022-07-25 hw: dix schematic conflict
    [connectors.kicad_sch, sensing.kicad_sch, stepper_testbench.kicad_sch]
2022-07-25 hw: fix pcb conflict
    [stepper_testbench.kicad_pcb]
2022-07-26 hw: first pcb routing
    [CAS 6-15-25-50-NP Blackbox.stp, stepper_testbench.kicad_pcb, stepper_testbench.kicad_sch]
2022-07-26 hw: update layout corrections
    [CAS 6-15-25-50-NP Blackbox.stp, connectors.kicad_sch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]
2022-07-26 fw: add pwm output
2022-07-26 hw: add bom
    [stepper_testbench.csv]
2022-07-27 hw: add round corners and credits
    [stepper_testbench.kicad_pcb]
2022-07-27 hw: add library folder
    [CAS 6-15-25-50-NP Blackbox.stp]
2022-07-27 hw: update layout with right screw terminal
    [connectors.kicad_sch, stepper_testbench.kicad_pcb, stepper_testbench.kicad_sch]
2022-07-27 hw: update layout
    [stepper_testbench.kicad_pcb]
2022-07-27 change 24V zener footprint to SMA
    [power.kicad_sch, stepper_testbench.kicad_pcb, stepper_testbench.kicad_sch]
2022-07-27 hw: sch update
    [power.kicad_sch, stepper_testbench.kicad_sch]
2022-07-28 fw: add stb master readme with flowchart
2022-07-28 hw: final pdf schematic upload
    [connectors.kicad_sch, power.kicad_sch, sensing.kicad_sch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]
2022-07-28 GUI: add motor models file
2022-07-28 hw: layout v0.1.1
    [connectors.kicad_sch, power.kicad_sch, sensing.kicad_sch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]
2022-07-28 hw: layout v0.1.2
    [stepper_testbench.kicad_pcb]
2022-07-28 hw: add gerber files
    [stepper_testbench-B_Cu.gbr, stepper_testbench-B_Mask.gbr, stepper_testbench-B_Paste.gbr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]
2022-07-28 GUI: add some params for voltage and current mode
2022-07-30 GUI: improved file management + motor configuration
    [motor_params.json]
2022-07-30 GUI: fix read error
    [main.py, motor_config.py]
2022-07-31 GUI: show device name when serial socket is open
2022-08-01 GUI: add <print_current_config> button
2022-08-01 GUI+fw: add basic float rx for slave device
2022-08-02 GUI: add brake buttons
2022-08-02 fw: add magnetic brake utils
2022-08-04 GUI: add fw/bw/hd/st/gt/gh buttons with cmd generation
2022-08-05 GUI: change motor generic commands to horizontal layout
2022-08-05 GUI: add dynamic text with pwm value received by master
2022-08-05 fw: add state machine + tx pwm value to gui
2022-08-05 GUI: add automatic test button
2022-08-07 GUI: change working mode (voltage/current) following powerstep01_CmVm_t enum
2022-08-07 GUI: add decay/fall enums in current params
2022-08-07 GUI: add motor config serialization (to be tested)
2022-08-09 fw master: add basic adc conversion + fix dma issue changing .ld file
    [STB-master.ioc, adc.c, main.c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]
2022-08-17 fw f7/f4: add tiny stb project with torque adc read
2022-08-17 GUI: BREAKING CHANGE - add thread and basic w/r csv based on torque value
2022-08-23 FW master: BREAKING CHANGE -> moved to STM32F746ZG (adc meas tested)
2022-08-23 GUI+FW: automated test basic version (no timer)
2022-08-25 fw+GUI: working prototype with automatic test
2022-08-25 fw+GUI: add manual test with adc output functionality
2022-08-26 fix: adc trigger timer is now at 200 Hz
    [STB-master.ioc, adc.c, main.c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]
2022-08-30 fw: add enable stepper supply before
2022-08-30 fix: add drivers folder
2022-10-20 BREAKING CHANGE: removed H7 board support
2022-10-20 BREAKING CHANGE: move to revised pcb layout
    [stepper_testbench-B_Cu.gbr, stepper_testbench-B_Mask.gbr, stepper_testbench-B_Paste.gbr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]

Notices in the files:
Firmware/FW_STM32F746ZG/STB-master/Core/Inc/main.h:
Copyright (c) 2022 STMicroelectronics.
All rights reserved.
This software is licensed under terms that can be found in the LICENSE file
